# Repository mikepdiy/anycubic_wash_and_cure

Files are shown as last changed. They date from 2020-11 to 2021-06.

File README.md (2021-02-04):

<b>What is this board?</b>

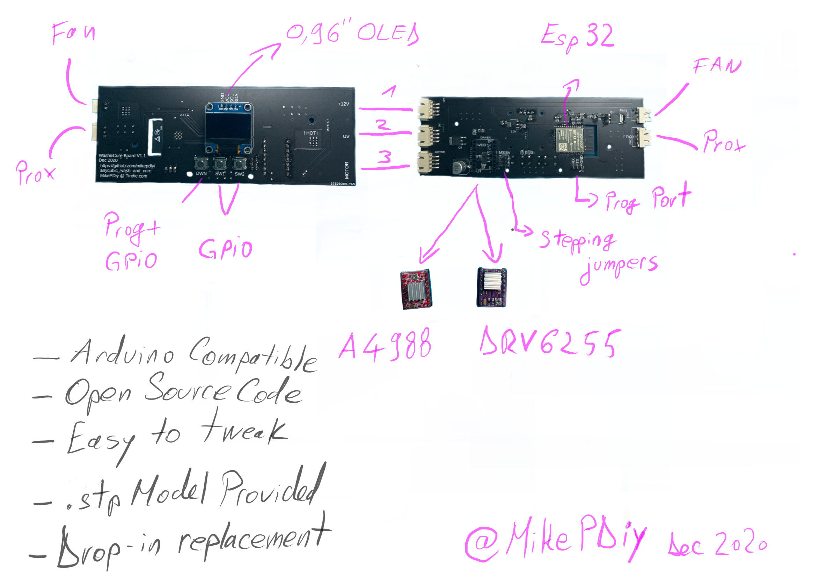
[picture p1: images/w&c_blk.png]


This is a drop in replacement board for the Anycubic Wash and Cure station that is used in conjunction with resin 3D Printers to clean and cure the resin prints after removing them form the printer. 

<b>How did this board came to life ?</b>

For some of my projects I am using resing 3D printing and I have to use the Anycubic Wash and Cure station extensively but something about it was not quite how I needed it and I decided to fix the problem myself. 

<b>My personal issues with the original board : </b>

1. In my workflow, I need to cure the resin for 8 minutes but the original board allows only to set 2 , 4 or 6 minutes. 
2. It always starts when powered up on CURE and not on Washing. I had many times pressed start forgetting I had to switch to wash so I messed a bit my prints. 
3. I have my printing setup in a location outside and not near my desk so I wanted a way to get informed when the curing or washing was done ( I hate to waste time near the printer and hearing the buzzer sound is not possible from my desk) . 

So not so many issues but using the machine very often these became real issues for my workflow . 

<b>What the new board does : </b>
1. Starts and allows you to decide what you want to do ( wash or cure) and to do that you just need to press the corresponding button for Wash or Cure . 
2. Uses wi-fi to create an Acces Point to which you can connect to configure the time for washing and curing from a nice web interface . (you can also programm it to connect to your own wi-fi network).
3. Maintains all the functionality of the original board in terms of safety.
4. Adds and OLED Display that give information about the ongoing process but also about the process of pairing the station to the Wi-fi Network. 
5. Allows any person with the knowledge to imrpove the software and share with the others . 
6. Comes with a basic but fully functional software preladed and tested . 
7. Fully coated in anti corosive material "just in case" .

<b>Why to buy this board ? </b>

Well, that would help me and allow me to keep developing boards like this while improving the board I have already made . 
This board in conjuction with some Arduino knowledge will allow you to tailor the way it works to perfectly fit your workflow just like you can do in FDM printing with the after market boards. 
The software and the pinout of the board is open sourced and you can see all the details you need here in order to play with the software yourself. 
Of course I can not be held responsible if you damage the board while doing this but I can give you some tips like : Make sure the UV and FAN pins are allways pulled low when your program starts or otherwise it will damage the mosfet and you will need to replace it. 

<b> Board specifications :</b>

Controller/ Processor : ESP32 ( Dual core version)

Motor Driver : Stick driver compatible with A4988 or DRV8825 ( Comes with A4988)

Input Power : 12V DC

Screen : 0,96' Monchrome OLED

Configurable buttons : 3 ( 1 acts also a programming mode button) 

Switching for UV and Fan : Thru Mosfets triggered by GPIO Pins

Programming port : 3 pin RS232 @3.3v (RX,TX,GND)

Same ports(and connectors) as the original board from the Wash and Cure .

<b> Needed software and libraries to work with this board : </b>

IDE : Arduino 1.8.3 ( I assume it will work with others like PlatformIO but I have not tested it so I warrant for Arduino IDE on Windows 10 , MacOS Catalina and linux flavours based on Ubuntu 20.04)

Board BSP : ESP32

Libraries : 

-ESPUI

-AccelStepper v1.61

-Adafruit SSD 1306

-Adafvruit GFX

-DNSServer ( possibly included in the ESP32 BSP)

<b> Where to buy the board </b>

https://www.tindie.com/products/22251/ </br>

</br>


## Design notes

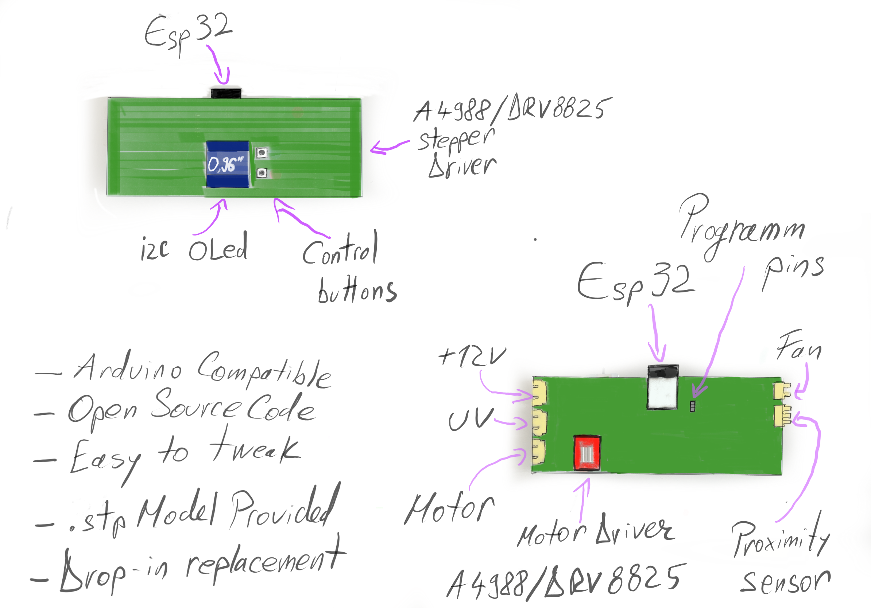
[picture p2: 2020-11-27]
images/w&c.PNG

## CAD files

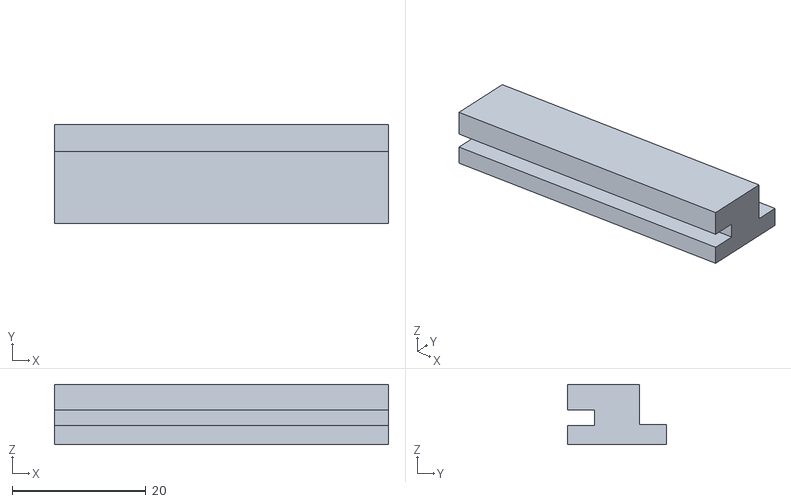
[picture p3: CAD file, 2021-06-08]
pcb holders/Body12.stl
50.0 x 14.8 x 9.00

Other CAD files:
pcb holders/Body11.stl

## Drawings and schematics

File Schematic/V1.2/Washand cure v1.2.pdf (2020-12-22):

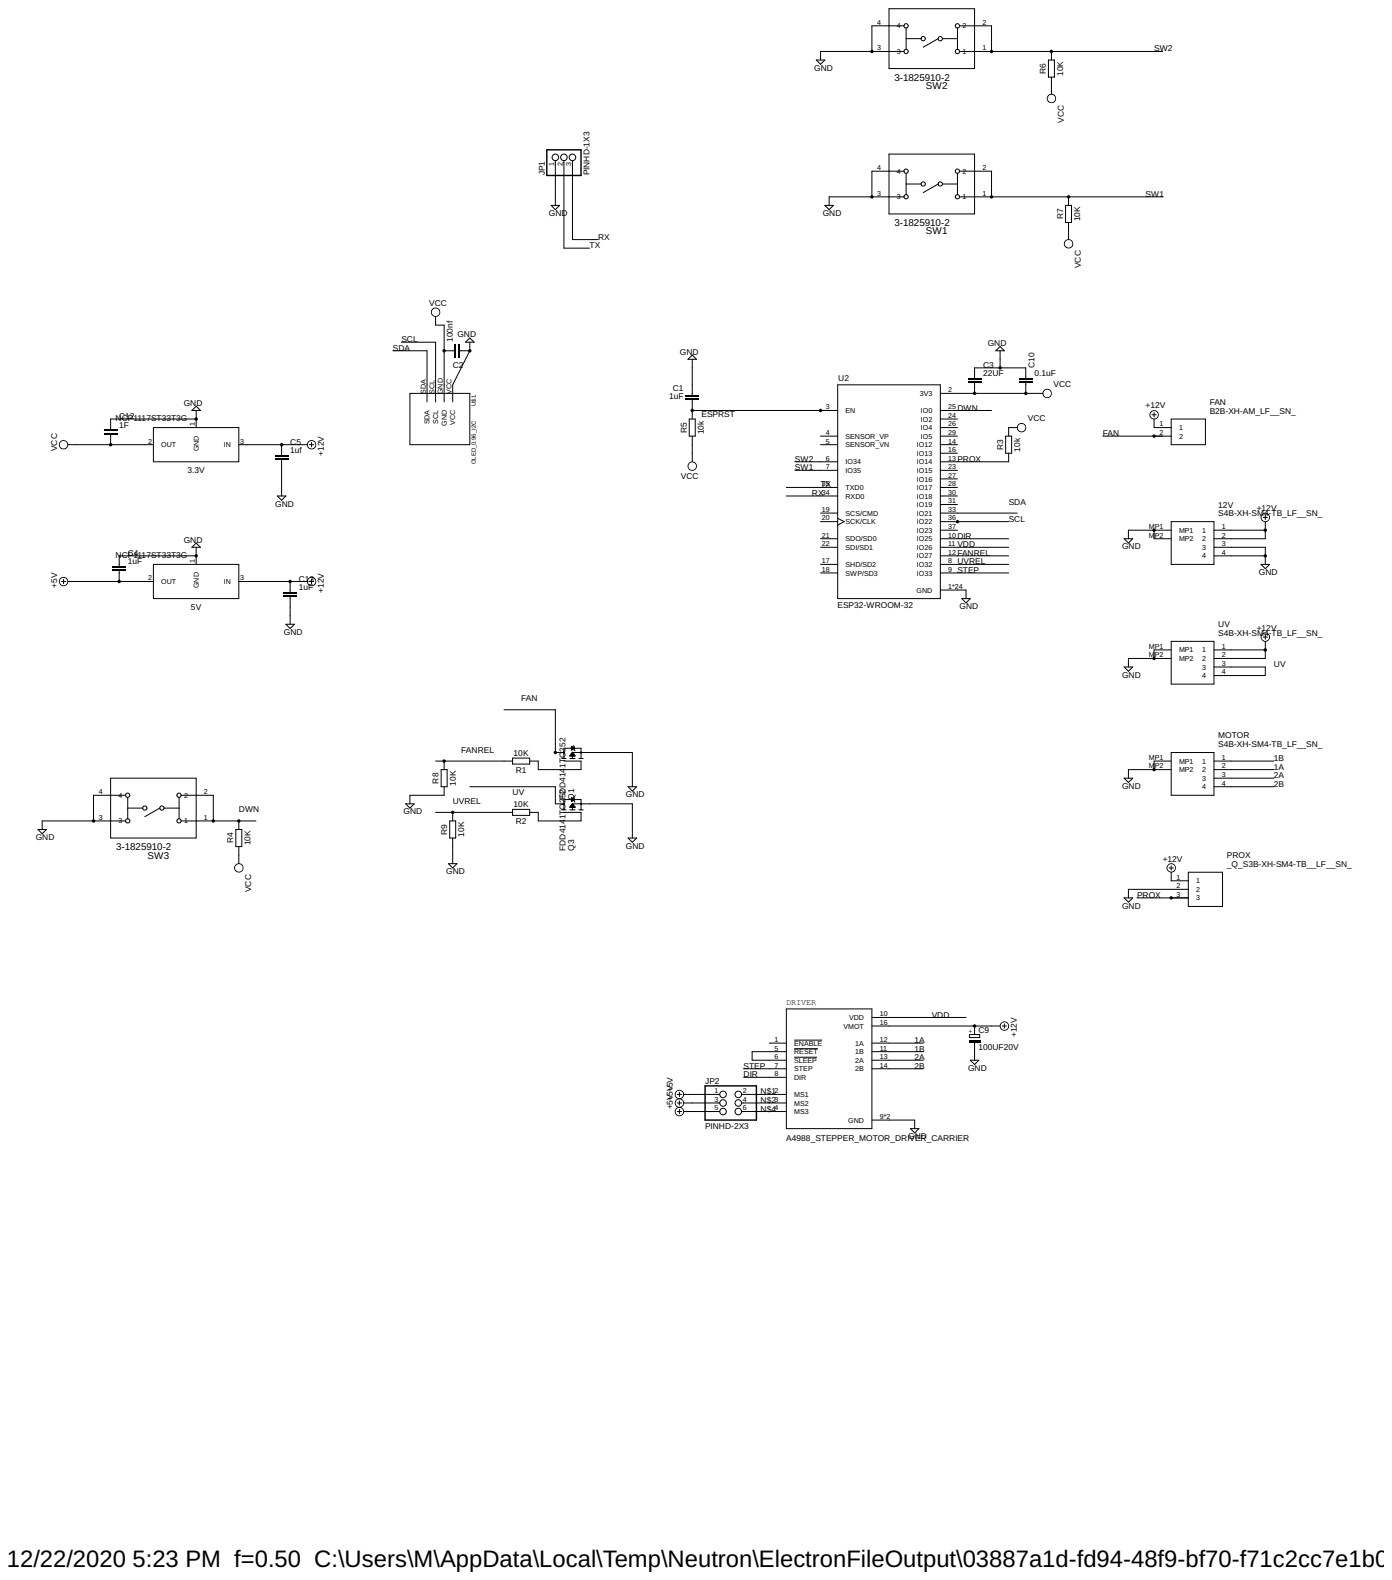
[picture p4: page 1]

12/22/2020 5:23 PM f=0.50 C:\Users\M\AppData\Local\Temp\Neutron\ElectronFileOutput\03887a1d-fd94-48f9-bf70-f71c2cc7e1b0\Washand cure v48.sch (Sheet: 1/1)

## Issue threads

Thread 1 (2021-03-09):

Any progress with changing the wash direction mid term?

rkolbi, 2021-03-09:
Hi,
Was wondering if you made any progress with changing the wash direction mid-term. Maybe it would be easier to change the direction every few minutes, using a sort of flip-flop logic?

rkolbi, 2021-03-09:
Here is an idea I have to change the direction half-way through. I haven't tested it as I don't yet have the board - this is just something I wrote in notepad.
```
~line 453
  if(washTimer == true && (now - lastTrigger > (washSeconds*1000))) {
  Serial.println("Washing stopped by timer…");
  washoff();
  }

Replace with:
  if(washTimer == true && (now - lastTrigger > (washSeconds*1000))) {
  Serial.println("Washing stopped by timer…");
  washoff();
  }

  if(washTimer == true && (now - lastTrigger > (washSeconds*500)) && (now - lastTrigger < (1000+(washSeconds*500)))) {
  Serial.println("Changing wash direction…");
  digitalWrite(motorEnable, LOW); // turn off the motor
  delay(1000);
  digitalWrite(motorEnable, HIGH); // enable the motor
  stepper.setSpeed(-16000); // set the motor speed in reverse
  stepper.runSpeed(); // restart the motor
  display.println("Washing.");
  }
```

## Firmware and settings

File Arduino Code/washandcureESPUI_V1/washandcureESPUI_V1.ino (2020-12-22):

//ToDO
//1. AP that can search for networks to connect to
//2. Change wash direction mid term


// include library to read and write from flash memory
#include <EEPROM.h>
#include <Bounce2.h>
#include <DNSServer.h>
#include <ESPUI.h>

//define Hotspot IP and DNS port
const byte DNS_PORT = 53;
IPAddress apIP(192, 168, 1, 1);
DNSServer dnsServer;

#if defined(ESP32)
#include <WiFi.h>
#else
#include <ESP8266WiFi.h>
#endif

//define your wi-fi network credentials
const char* ssid     = "W&C";
const char* password = "washandcure";



//define AP hostname
const char *hostname = "wash&cure";


// define the number of bytes we want to access in the EEPROM to save the Wash and cure time
#define EEPROM_SIZE 2
int WashValue;   // store the curing and wash timer value
int CureValue;   // store the curing and wash timer value


// Include the AccelStepper library:
#include <AccelStepper.h>
// Define stepper motor connections and motor interface type. Motor interface type must be set to 1 when using a driver:
#define dirPin 25 // driver stick DIR pin
#define stepPin 33 // // driver stick STP pin
#define motorInterfaceType 1
#define motorEnable 26 // driver stick VDD pin
#define UvPin  32    //UV Pin
#define FanPin  27     //Fan  pin 
#define SW1  35     //SW1 Button 
#define SW2  34     //SW2 Button 
#define SW3  0      //SW3 Button . Used for programming mode also .
int IRInputPin = 14; //Proximity Sensor for the LID
int IROutputState;  //Proximity Sensor state

//enable Bounce on the 3 GPIO pins: SW1,SW2,DWN
Bounce debouncer1 = Bounce(); 
Bounce debouncer2 = Bounce(); 
Bounce debouncer3 = Bounce(); 

//OLED libraries and settings
#include <Wire.h>
#include <Adafruit_GFX.h>
#include <Adafruit_SSD1306.h>
#define SCREEN_WIDTH 128 // OLED display width, in pixels
#define SCREEN_HEIGHT 64 // OLED display height, in pixels

// Declaration for an SSD1306 display connected to I2C (SDA, SCL pins)
Adafruit_SSD1306 display(SCREEN_WIDTH, SCREEN_HEIGHT, &Wire, -1);


// Create a new instance of the AccelStepper class:
AccelStepper stepper = AccelStepper(motorInterfaceType, stepPin, dirPin);



int statusLabelId;
int millisLabelId;
int WashSwitchId;
int UvSwitchId;
static bool WashSwitchState = false;
static bool UvSwitchState = false;

//Timer variables

// for Washing Cycle
int washSeconds ;
unsigned long now = millis();
unsigned long lastTrigger = 0;
boolean washTimer = false;

// for UV Curing Cycle
int uvSeconds ;
boolean uvTimer = false;

//add slider for timing
void slider(Control *sender, int type) {
  Serial.print("Slider: ID: ");
  Serial.print(sender->id);
  Serial.print(", Value: ");
  Serial.println(sender->value);
  // Like all Control Values in ESPUI slider values are Strings. To use them as int simply do this:
  int WashValueWithOffset = sender->value.toInt();
  // save the timer value in flash memory
    EEPROM.write(0, WashValueWithOffset);
    EEPROM.commit();
    Serial.println("level saved in flash memory");
    WashValue = EEPROM.read(0);
    Serial.println("Wash value from memory");
    Serial.println(WashValue);
    washSeconds = WashValue*60 ;
}

void slider2(Control *sender, int type) {
  Serial.print("Slider: ID: ");
  Serial.print(sender->id);
  Serial.print(", Value: ");
  Serial.println(sender->value);
  // Like all Control Values in ESPUI slider values are Strings. To use them as int simply do this:
  int CureValueWithOffset = sender->value.toInt();
  // save the timer value in flash memory
    EEPROM.write(1, CureValueWithOffset);
    EEPROM.commit();
    Serial.println("level saved in flash memory");
    CureValue = EEPROM.read(1);
    Serial.println("Cure value from memory");
    Serial.println(CureValue);
    uvSeconds = CureValue*60 ;
}


void numberCall(Control *sender, int type) { Serial.println(sender->value); }

void switchExample(Control *sender, int value) {
  switch (value) {
  case S_ACTIVE:
  //WashSwitchState = true;
    Serial.print("Active:");
     ESPUI.print(statusLabelId, "Wash Active");
   wash();
    break;

  case S_INACTIVE:
 // WashSwitchState = false;
    Serial.print("Inactive");
     ESPUI.print(statusLabelId, "Ready");
    washoff();
    break;
  }

  Serial.print(" ");
  Serial.println(sender->id);
}

void otherSwitchExample(Control *sender, int value) {
  switch (value) {
  case S_ACTIVE:
    Serial.print("Active:");
    ESPUI.print(statusLabelId, "Cure Active");
    cure();
    break;

  case S_INACTIVE:
    Serial.print("Inactive");
    ESPUI.print(statusLabelId, "Ready");
    cureoff();
    break;
  }

  Serial.print(" ");
  Serial.println(sender->id);
}


void wash( ) {
  Serial.println("Wash Cycle ON !");
   WashValue = EEPROM.read(0);
    Serial.println("Wash value from memory");
    Serial.println(WashValue);
    washSeconds = WashValue*60 ;
   //WashSwitchState = true;
   washTimer = true; // start the washing timer
   lastTrigger = millis(); 
   digitalWrite(FanPin, HIGH); //turn on the fan
   digitalWrite(motorEnable, HIGH); // enable the motor
   
   stepper.setSpeed(16000); // set the motor speed
   stepper.runSpeed(); // start the motor

   //Handle the OLED screen
  display.clearDisplay();
  display.setTextSize(2);
  display.setTextColor(WHITE);
  display.setCursor(0, 10);
  // Display static text
  display.println("Washing");
  display.display(); 
   
  return;
  }
 void washoff(){
  
   ESPUI.print(statusLabelId, "Ready");
  digitalWrite(FanPin, LOW); // turn off the fan
  digitalWrite(motorEnable, LOW); // turn off the motor
  
   WashSwitchState = false;
   ESPUI.updateSwitcher(WashSwitchId, WashSwitchState);

  washTimer = false; // stop the timer
  Serial.println("Wash Cycle Finished!Returning to main loop");
  //handle the OLED screen
  display.clearDisplay();
  display.setTextSize(2);
  display.setTextColor(WHITE);
  display.setCursor(0, 10);
  // Display static text
  display.println("Washing");
  display.print(" Done !");
  display.display(); 
  return;

}

void cure()
{ 
  
   Serial.println("UV Cycle ON !");
    CureValue = EEPROM.read(1);
    Serial.println("Cure value from memory");
    Serial.println(CureValue);
    uvSeconds = CureValue*60 ;
   uvTimer = true; // start the UV timer
   lastTrigger = millis();
   
  digitalWrite(motorEnable, HIGH); // turn on the motor
  digitalWrite(FanPin, HIGH); // turn on the fan
  digitalWrite(UvPin, HIGH); // turn on the UV lamp
  stepper.setSpeed(500); // set the motor speed
  stepper.runSpeed(); // start the motor
  
  //handle the OLED screen
  display.clearDisplay();
  delay(5);
  display.setTextSize(2);
  display.setTextColor(WHITE);
  display.setCursor(1, 10);
  
  // Display static text
  display.println("UV Curing");
  display.display(); 
  // ESP.wdtFeed();
 


}
void cureoff(){
UvSwitchState = false;
ESPUI.updateSwitcher(UvSwitchId, UvSwitchState);
ESPUI.print(statusLabelId, "Ready");
digitalWrite(UvPin, LOW); // turn off UV
digitalWrite(FanPin, LOW);  // turn off the fan
digitalWrite(motorEnable, LOW); // turn off the motor

uvTimer = false; // stop the UV timer

Serial.println("UV Cycle Finished!Returning to main loop");
// handle the oled screen
  display.clearDisplay();
  delay(5);
  display.setTextSize(2);
  display.setTextColor(WHITE);
  display.setCursor(0, 10);
  
  // Display static text
  display.println("Curing ");
  display.print(" Done !");
  display.display(); 
return;
}

void StopAll() {
cureoff();
washoff();

Serial.println("The lid is not set !");
// handle the oled screen
  display.clearDisplay();
  delay(5);
  display.setTextSize(3);
  display.setTextColor(WHITE);
  display.setCursor(0, 10);
  
  // Display static text
  display.println("LID!");
 //display.print(" Done !");
  display.display(); 
return;

}


void setup(void) {
    // initialize EEPROM with predefined size
     EEPROM.begin(EEPROM_SIZE);
     WashValue = EEPROM.read(0);
     CureValue = EEPROM.read(1);
  Serial.begin(115200);

  // define the GPIO functions
  pinMode(IRInputPin, INPUT);
  pinMode(motorEnable, OUTPUT);
  pinMode(UvPin, OUTPUT);
  pinMode(FanPin, OUTPUT);
  pinMode(SW1, INPUT);
  pinMode(SW2, INPUT);      
  pinMode(SW3, INPUT);     
  //define the GPIO initial states
  digitalWrite(motorEnable, LOW);
  //!!!!!!!!!!!!!!!!!!!!!!!!!!!!!!!!!!!!!!!!!!!!!!!!!!!!!!!!!!!!!!!!!!!!!!!!!!!!!!!!!!!!!!
  digitalWrite(UvPin, LOW); // NEVER SET THIS HIGH ! IT WILL DAMAGE THE MOSFET AND YOU WILL HAVE TO REPLACE IT !
  digitalWrite(FanPin, LOW); //NEVER SET THIS HIGH ! IT WILL DAMAGE THE MOSFET AND YOU WILL HAVE TO REPLACE IT !
  //!!!!!!!!!!!!!!!!!!!!!!!!!!!!!!!!!!!!!!!!!!!!!!!!!!!!!!!!!!!!!!!!!!!!!!!!!!!!!!!!!!!!!!
  debouncer1.attach(SW1);
  debouncer1.interval(5); // interval in ms
  debouncer2.attach(SW2);
  debouncer2.interval(5); // interval in ms
  debouncer3.attach(SW3);
  debouncer3.interval(5); // interval in ms
  
  stepper.setMaxSpeed(16000); // set motor max speed
  stepper.setAcceleration(100); // set motor acceleration
  
  ///OLED setup
  Wire.begin(21,22);//OLED I2C Pins
  if(!display.begin(SSD1306_SWITCHCAPVCC, 0x3C)) { // Address for the I2C OLED screen
    Serial.println(F("SSD1306 allocation failed"));
    for(;;);
  }
  delay(2000);
  display.clearDisplay();
  display.setTextSize(2);
  display.setTextColor(WHITE);
  display.setCursor(0, 10);
  
  // Display static text
  display.println("Powering ");
  display.print(" UP ");
  display.display(); 
  ESPUI.setVerbosity(Verbosity::VerboseJSON);



#if defined(ESP32)
  WiFi.setHostname(hostname);
#else
  WiFi.hostname(hostname);
#endif

  // try to connect to existing network
  WiFi.begin(ssid, password);
  Serial.print("\n\nTry to connect to existing network");

  {
    uint8_t timeout = 10;

    // Wait for connection, 5s timeout
    do {
      delay(500);
      Serial.print(".");
      timeout--;
    } while (timeout && WiFi.status() != WL_CONNECTED);

    // not connected -> create hotspot
    if (WiFi.status() != WL_CONNECTED) {
      Serial.print("\n\nCreating hotspot");

      WiFi.mode(WIFI_AP);
      WiFi.softAPConfig(apIP, apIP, IPAddress(255, 255, 255, 0));
      WiFi.softAP(ssid);

      timeout = 5;

      do {
        delay(500);
        Serial.print(".");
        timeout--;
      } while (timeout);
    }
  }

  dnsServer.start(DNS_PORT, "*", apIP);

  Serial.println("\n\nWiFi parameters:");
  Serial.print("Mode: ");
  Serial.println(WiFi.getMode() == WIFI_AP ? "Station" : "Client");
  Serial.print("IP address: ");
  Serial.println(WiFi.getMode() == WIFI_AP ? WiFi.softAPIP() : WiFi.localIP());
  //display Wi-Fi mode and IP address
  delay(2000);
  display.clearDisplay();
  display.setTextSize(2);
  display.setTextColor(WHITE);
  display.setCursor(0, 10);
  
  // Display static text
  display.println(WiFi.getMode() == WIFI_AP ? "Station" : "Client");
  display.setTextSize(1);
  display.print("IP: ");
  display.println(WiFi.getMode() == WIFI_AP ? WiFi.softAPIP() : WiFi.localIP());
  display.display(); 
  
  statusLabelId = ESPUI.label("Status:", ControlColor::Sunflower, "Ready");
  WashSwitchId = ESPUI.switcher("Wash", &switchExample, ControlColor::Peterriver, false);
  ESPUI.slider("Wash Duration (minutes): ", &slider, ControlColor::Peterriver, WashValue, 1,15);
  UvSwitchId = ESPUI.switcher("Cure", &otherSwitchExample, ControlColor::Emerald, false);
  ESPUI.slider("Cure Duration (minutes): ", &slider2, ControlColor::Emerald, CureValue, 1,15);


  /*
   * .begin loads and serves all files from PROGMEM directly.
   * If you want to serve the files from SPIFFS use ESPUI.beginSPIFFS
   * (.prepareFileSystem has to be run in an empty sketch before)
   */
 
  // Enable this option if you want sliders to be continuous (update during move) and not discrete (update on stop)
  // ESPUI.sliderContinuous = true;

  /*
   * Optionally you can use HTTP BasicAuth. Keep in mind that this is NOT a
   * SECURE way of limiting access.
   * Anyone who is able to sniff traffic will be able to intercept your password
   * since it is transmitted in cleartext. Just add a string as username and
   * password, for example begin("ESPUI Control", "username", "password")
   */
  ESPUI.begin("Wash and Cure Station");

}

void loop(void) {
  dnsServer.processNextRequest();
  now = millis();

IROutputState = digitalRead(IRInputPin);
  //Check if the lid is on the wash and cure machine at all times. If the lid is not present or removed, stop the machine immediately. 
  if ( IROutputState == HIGH && washTimer == true || IROutputState == HIGH && uvTimer == true) {
    
    StopAll();
  }
else {
 
}

  
  if(washTimer == true && (now - lastTrigger > (washSeconds*1000))) {
  Serial.println("Washing stopped by timer…");
  washoff();
  }
    if(uvTimer == true && (now - lastTrigger > (uvSeconds*1000))) {
  Serial.println("UV Cure stopped by timer…");
  cureoff();

}
  // Update the Bounce instances :
  debouncer1.update();
  debouncer2.update();
  debouncer3.update(); 
  int value1 = debouncer1.read();
  int value2 = debouncer2.read();
  int value3 = debouncer3.read();
  


if (debouncer1.fell() && washTimer == false && uvTimer == false)
{
  cure();
}
else if( debouncer1.fell() && washTimer == true && uvTimer == false )
{
washoff();
delay(1);
//cure();
}
else if( debouncer1.fell() && washTimer == false && uvTimer == true )
{
cureoff();
delay(1);
}
else
{
  // action B
}

if (debouncer2.fell() && uvTimer == false && washTimer == false  )
{
  wash();
}
else if( debouncer2.fell() && uvTimer == true && washTimer == false  )
{
cureoff();
delay(1);
//wash();
}
else if( debouncer2.fell() && uvTimer == false && washTimer == true  )
{

washoff();
}
else
{
  // action B
}
if (debouncer3.fell() && washTimer == true && uvTimer == false)
{
washoff();
}
else if( debouncer3.fell() && washTimer == false && uvTimer == true )
{
cureoff();
delay(1);
//cure();
}
else if( debouncer3.fell() && washTimer == false && uvTimer == false ) // display the network status
{
display.clearDisplay();
  display.setTextSize(2);
  display.setTextColor(WHITE);
  display.setCursor(0, 10);
  
  // Display static text
  display.println(WiFi.getMode() == WIFI_AP ? "Station" : "Client");
  display.setTextSize(1);
  display.print("IP: ");
  display.println(WiFi.getMode() == WIFI_AP ? WiFi.softAPIP() : WiFi.localIP());
  display.display(); 
}
else
{
  // action B
}
stepper.runSpeed();
}

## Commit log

2020-12-02 Create Washand cure2 pcb v5.step
2020-12-22 add schematics and code
2021-01-12 Correction for schematic
2021-06-08 added pcb holders STL's
    [Body11.stl, Body12.stl]
